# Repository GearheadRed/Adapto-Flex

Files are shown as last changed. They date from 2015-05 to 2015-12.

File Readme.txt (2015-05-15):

Behold The ADAPTO FLEX!! http://reprap.org/wiki/Adapto_Flex
	Originated from the Adapto https://github.com/rotorit/Adapto

The thought behind the Adapto Flex is to support a more flexible variety of tool heads(thus Adapto Flex).

Currently the paste extruder mount and support for Mutley's Flex3Drive system(http://mutley3d.com/Flex3Drive/) exist in working complete tool head options. In the pipeline for mountable tool heads will be a dual extruder configuration, single extruder configuration, pen holder, and cable driven dremel mount(more suggestions and contributions welcome).

There are design changes with the Adapto Flex, notably implementing the Vertical X Standard(http://reprap.org/wiki/Vertical_X_Axis_Standard) and moving the Z axis smooth rods to the sides of the Z frame instead of in front of the Z frame. This has allowed for shrinking the X ends making them stronger with less material use, and relocating the belt and drive motor position to run between the X smooth rods.

The X carriage is a flat plate style with four bolt holes. This allows for mounting a variety of tool heads increasing the printers versatility. It is suggested to use a SmoothieBoard with the printer and leveraging the ability to swap out config files quickly and easily per tool head setup instead of having to re-flash the controller firmware each time you swap tool heads.

This design still retains the ability to use either Alu extrusions (20x20mm), wood, alu, acryl plates or plates made out of any material(if it is stiff enough). Smooth rods can still be of any length, however the upper cross frame piece must be the same length as the front and rear lower frame pieces now(X axis). It is recommended to use 20x20mm aluminum T-slot extrusion for the frame and 10mm smooth rods.

Example STLs have been provided to view the parts on github. Most parts are based on RoTorITs design but either combined to reduce part count, save plastic, or make the design more versatile. A few parts are t00ties designs or t00ties code re-structured to handle the central config file better(these files retain t00ties copyright headings in them).

On the todo list is:
  -Endstop holders

ENJOY!

Making the STLs
---------------
Edit ./inc/configuration.scad to suit your needs. Check the resulting parts for sanity.

On linux make the stls by typing one of
make -k
make -k -j12

If openscad is in your path this should result in lots of new files in the "output" directory.
The _x# in the file names is the amount of a given part that needs to be printed.

Creative Commons - GNU GPL license

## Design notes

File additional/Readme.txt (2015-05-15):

Additional Component parts and templates.

Files - Description

bedBlockBasic_x4.scad	-	basic corner blocks to support heated pcb and glass
bedBlockRetainer_x2.scad-	corner blocks with retaining tabs to hold down heated pcb and glass
bedHoles.dxf		-	defines holes for the base bed plate
bedHoles.scad		-	defines holes for the base bed plate
cornerBrace_x8.scad	-	corner braces for aluminum extrusions(metal corner braces are suggested)
Extruder.scad		-	minimalistic direct drive extruder[STILL IN DEVELOPMENT DO NOT USE]
Flex3DriveFan.scad	-	fan mount for use with Flex3DriveMount
Flex3DriveMount.scad	-	mount design to hold Mutleys Flex3Drive system to the xCarriage
IndicatorMount.scad	-	mount for basic digital/dial indicator, clamps to x carriage rods
SyringeMount.scad	-	holds a syringe to the xCarriage
zEndstop.scad		-	quick and dirty z endstop bracket

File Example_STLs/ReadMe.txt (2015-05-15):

These STLs were generated via openSCAD with the below settings in the ./inc/configuration.scad file.

!!!This is not likely default configuration for most users due to the ACME rod specs for the z axis but applies to GearheadRed's printer configuration specifically.

//====================//
// Basic Config Items //
//====================//
smoothRod=10;			// diameter of smooth rods in mm
linearBearing=lm10uu;		// change this to the linear bearing you are using from the definitions section
zRod=ACME14;			// change this to the z threaded rod you are using from the definitions section
zRodnut=ACME14nut;		// change this to the z nut you are using from the definitions section
zRodnutThickness=ACME14nutThickness;	// change this to the z nut thickness you are using from the definitions section

//=======================//
// Advanced Config Items //
//=======================//
$fn=200;			// default resolution for parts, decrease if part compiling or stl/gcode is unmanageable
thickness=5;			// thickness of walls etc. in parts
smoothRodOffset=thickness*2+2+smoothRod/2;	// how far the centre of the z smooth rods are from the frame

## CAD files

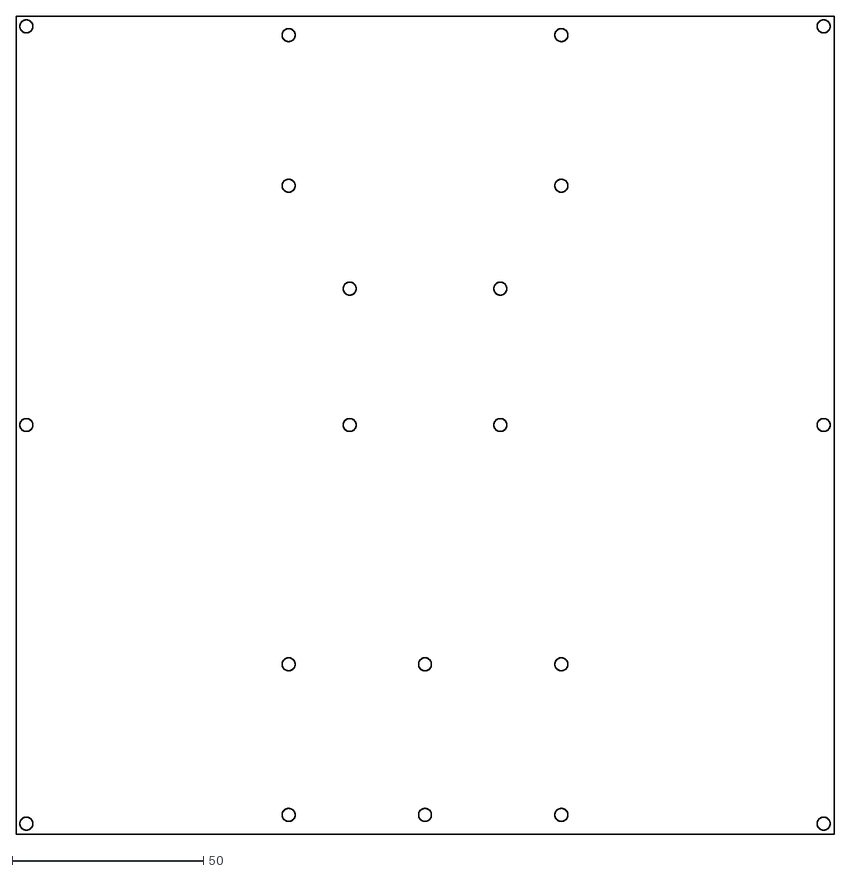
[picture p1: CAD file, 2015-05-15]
additional/bedHoles.dxf
214.0 x 214.0

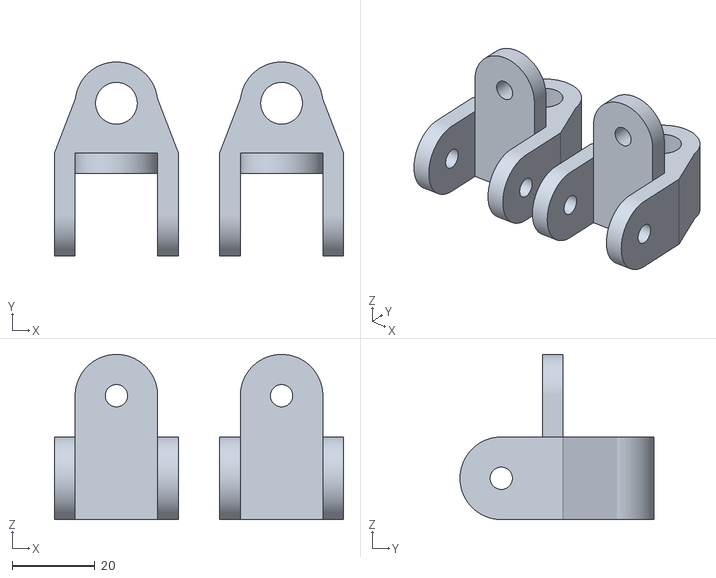
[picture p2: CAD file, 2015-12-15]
Example_STLs/zUpper_x1.stl
70.0 x 47.0 x 40.0

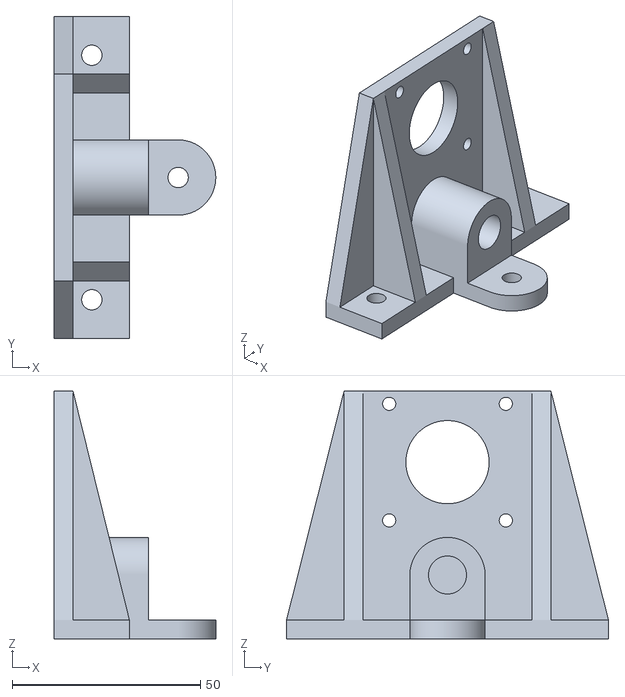
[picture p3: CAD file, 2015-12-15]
Example_STLs/zMotor_x2.stl
43.0 x 85.6 x 65.9

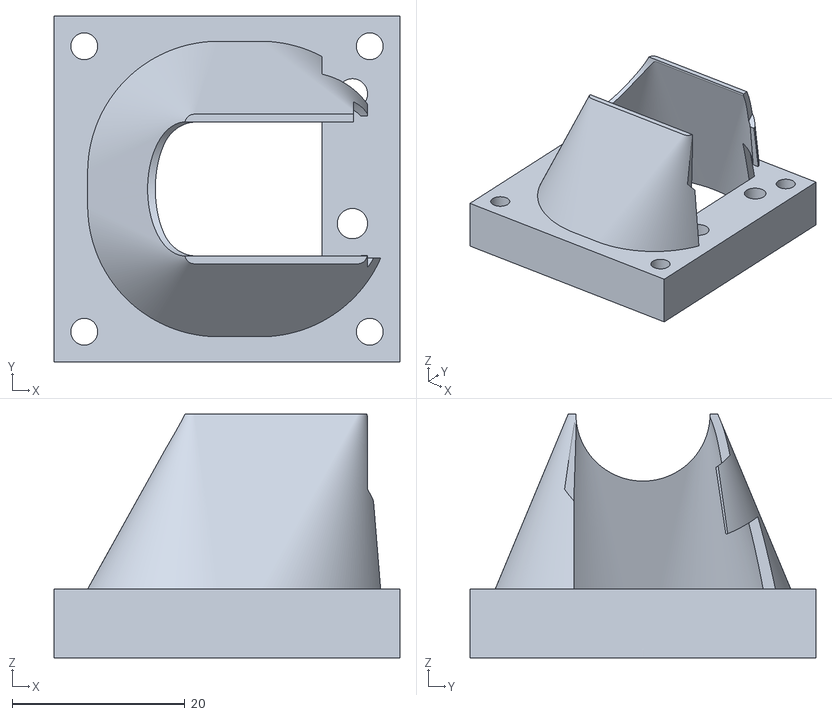
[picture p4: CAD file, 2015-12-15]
Example_STLs/Flex3DriveV2Fan.stl
40.0 x 40.0 x 28.2

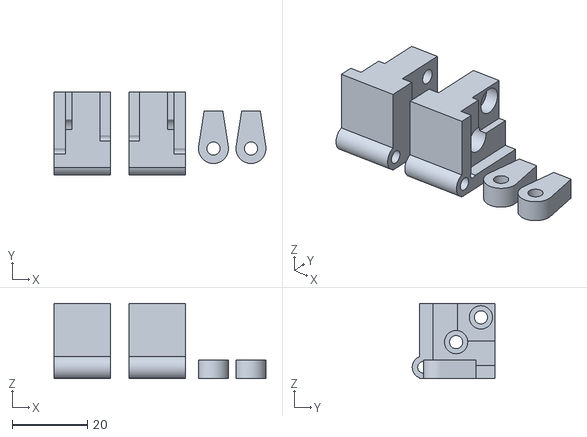
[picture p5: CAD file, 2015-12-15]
Example_STLs/bedBlockRetainer_custom.stl
56.5 x 22.0 x 20.0

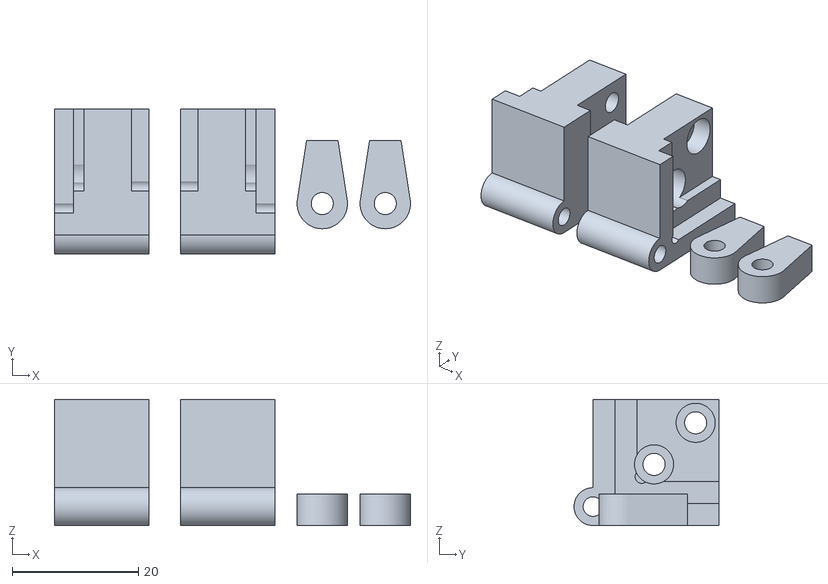
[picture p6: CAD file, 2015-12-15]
Example_STLs/bedBlockRetainer_x2.stl
56.5 x 23.0 x 20.0

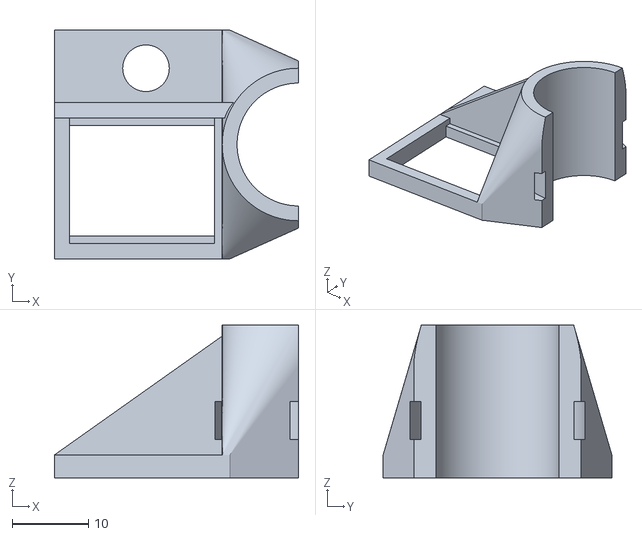
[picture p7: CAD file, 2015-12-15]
Example_STLs/hotendPower.stl
32.0 x 30.0 x 20.0

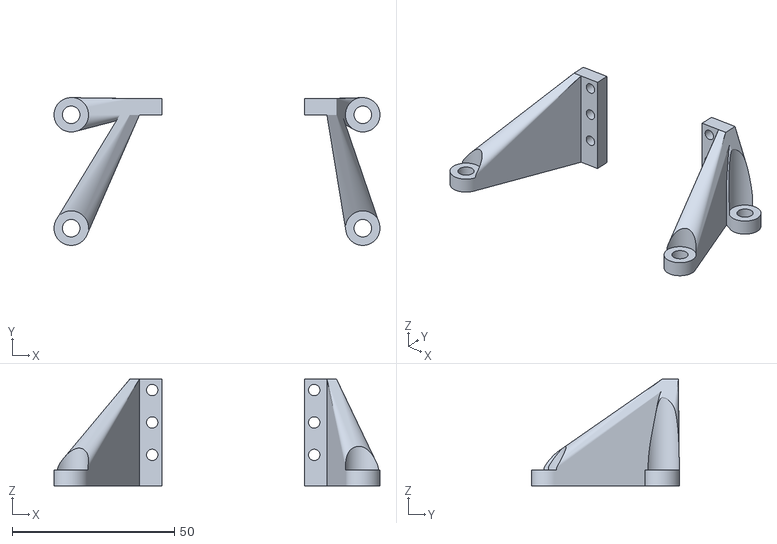
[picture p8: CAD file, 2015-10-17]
Example_STLs/Flex3DriveV2Mount.stl
100.6 x 45.6 x 33.0

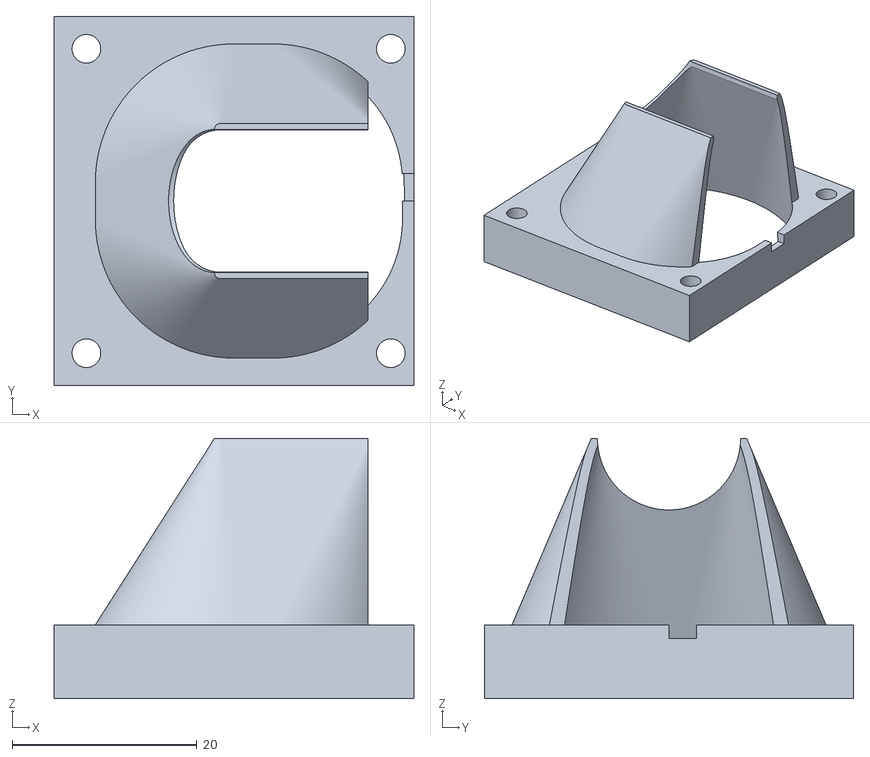
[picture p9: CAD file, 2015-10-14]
Example_STLs/Flex3DriveV1Fan.stl
39.0 x 40.0 x 28.2

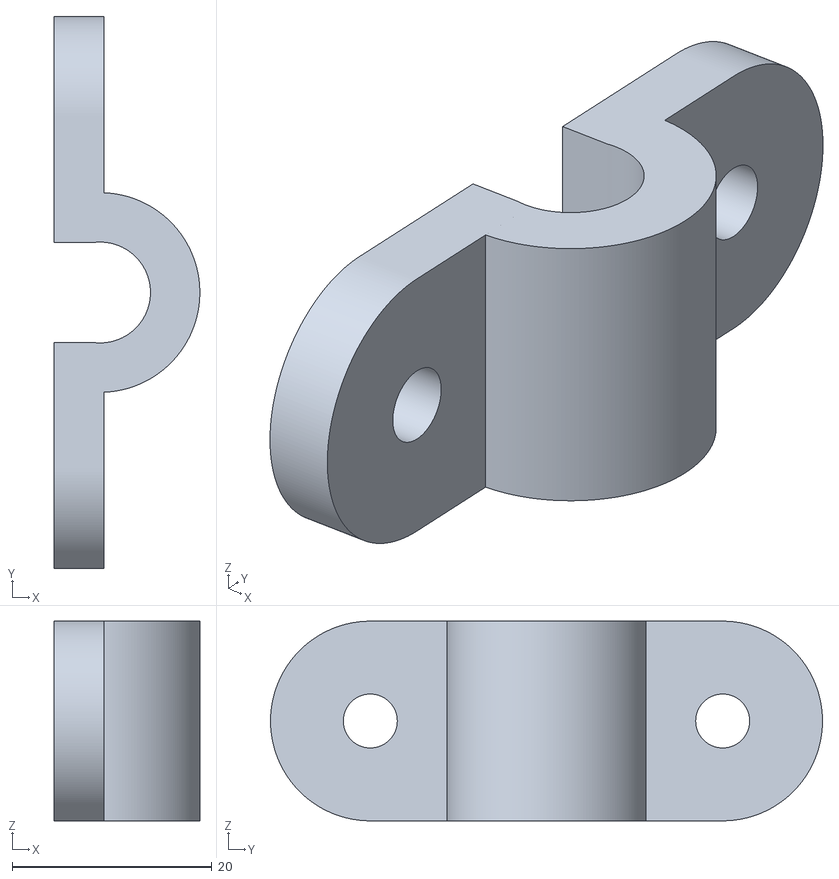
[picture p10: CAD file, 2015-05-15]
Example_STLs/yClamp_x4.stl
14.6 x 55.3 x 20.0

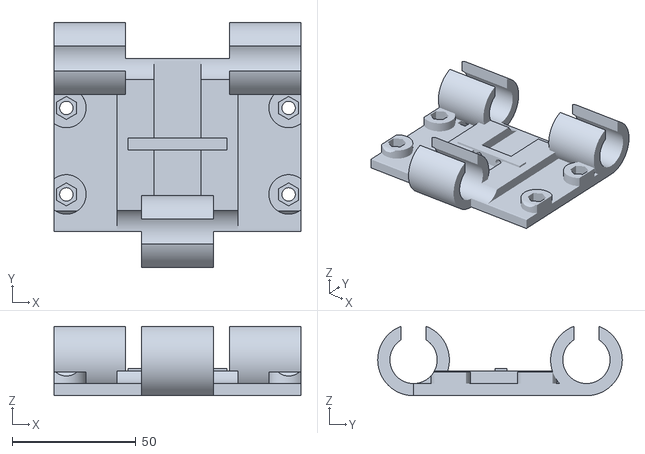
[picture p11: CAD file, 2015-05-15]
Example_STLs/xCarriage_x1.stl
100.0 x 99.0 x 28.1

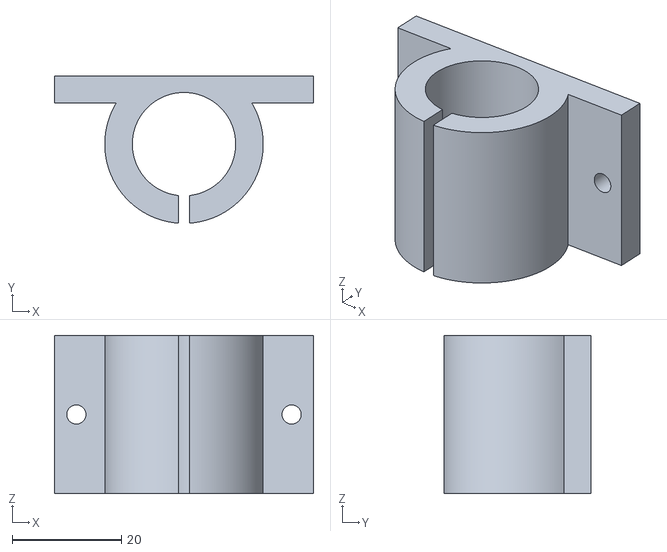
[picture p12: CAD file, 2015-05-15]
Example_STLs/yBearing_x4.stl
47.4 x 27.0 x 29.0

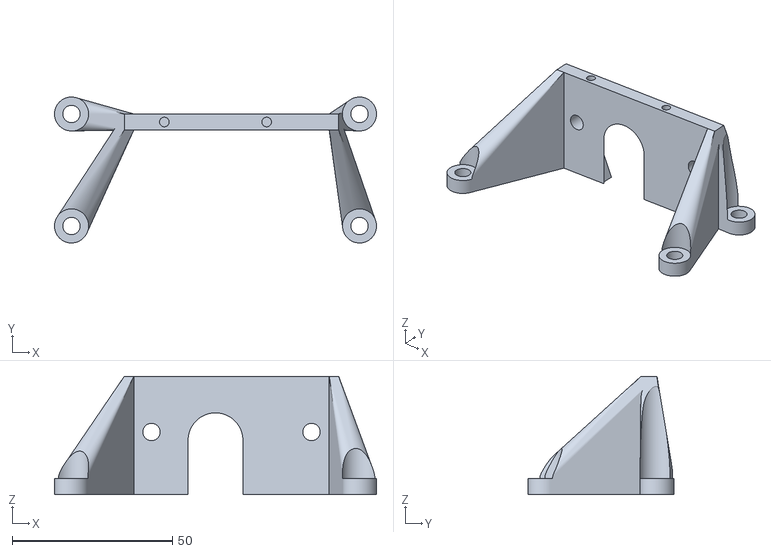
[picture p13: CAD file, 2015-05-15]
Example_STLs/Flex3DriveV1Mount.stl
100.6 x 45.6 x 37.0

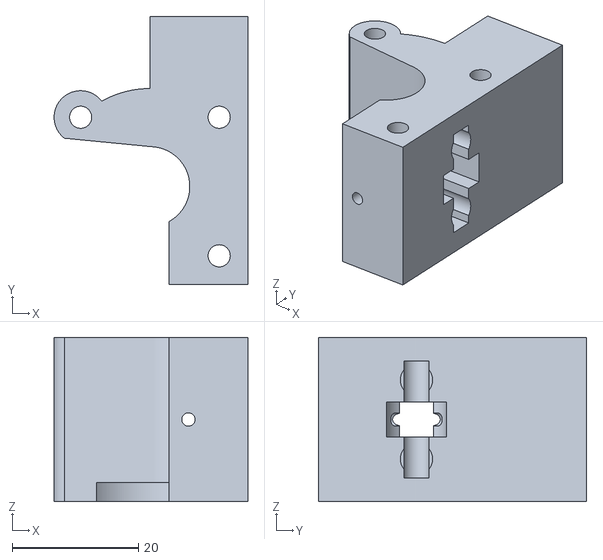
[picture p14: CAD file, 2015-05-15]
Example_STLs/Extruder_demo.stl
30.7 x 42.4 x 26.0

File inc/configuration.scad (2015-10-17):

// Adapto Flex is licensed under the Creative Commons - GNU GPL license.
// http://creativecommons.org/licenses/GPL/2.0/
// Originated from Adapto https://github.com/rotorit/Adapto

//==========================================================================//
// Configuration file for Adapto Flex OpenSCAD files                        //
// Scroll past the definition section to change basic and advanced settings //
//==========================================================================//

//====================//
// Definition Section //
//====================//
// Frame and Walls
// frameX and frameY are the dimensions of the frame material when viewed on end(the end of an extrusion looks roughly like an X)
// frameX is the width of the frame material
// frameY is the height of the frame material
//   x
//  [ ]y
// these are used to find offsets for screw placing so screws meet the (slot in the) middle of the frame
frameX=20;// width of the frame material(alu, wood etc.)
frameY=20;// height of the frame material

// Print the hole_calibration.scad object to dial in the next 6 settings
// Google found http://www.fairburyfastener.com/xdims_metric_nuts.htm
M8=8.4;// diameter of M8 threaded rod
M5=5.3;// diameter of M5 threaded rod
M3=3.4;// diameter of M3 threaded rod
M8nut=13;// diameter of M8 nut flat to flat
M5nut=8;// diameter of M5 nut flat to flat
M3nut=5.6;// diameter of M3 nut flat to flat

M8nutThickness=6.8;// thickness of a standard M8 nut(nylock is 8mm)
M5nutThickness=4.7;// thickness of a standard M5 nut(nylock is 5mm)
M3nutThickness=2.4;// thickness of a standard M3 nut

// Acme Linear Screw and Nut
ACME14=6.5;// diameter of 1/4 inch ACME threaded rod in mm
ACME14nut=12.8;// diameter of ACME 1/4 inch nut flat to flat in mm
ACME14nutThickness=6.5;// thickness of ACME 1/4 inch nut in mm

// Linear Bearings
// format is IDxODxL
lm8uu=[8, 15, 24];
lm10uu=[10, 19, 29];
lm10luu=[10, 19, 55];
lm12uu=[12, 21, 30];

//rotary bearings
// format is IDxODxL
FL623=[3, 10, 4];
MF204=[4, 10, 4];
MF126=[6, 12, 4];
rotaryBearing=MF126;// for readability(can be changed if other bearings are used

//====================//
// Basic Config Items //
//====================//
smoothRod=10;				// diameter of smooth rods in mm
linearBearing=lm10uu;	// change this to the linear bearing you are using from the definitions section
zRod=ACME14;				// change this to the z threaded rod you are using from the definitions section
zRodnut=ACME14nut;		// change this to the z nut you are using from the definitions section
zRodnutThickness=ACME14nutThickness;	// change this to the z nut thickness you are using from the definitions section

//=======================//
// Advanced Config Items //
//=======================//
$fn=250;		// default resolution for parts, decrease if part compiling or stl/gcode is unmanageable
thickness=5;		// thickness of walls etc. in parts
pullyDiameter=12.2;	// GT2-20 toothed section diameter
smoothRodOffset=thickness*2+2+smoothRod/2;	// how far the centre of the z smooth rods are from the frame
Flex3Drive=true;	// If the Flex3Drive is used
carriageDrop=15;	// From center of carriage to top mounting surface on extruder mounts

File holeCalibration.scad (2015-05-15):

// Adapto Flex is licensed under the Creative Commons - GNU GPL license.
// http://creativecommons.org/licenses/GPL/2.0/
// Originated from Adapto https://github.com/rotorit/Adapto
include <./inc/configuration.scad>
use <./inc/polyarc.scad>

// hole size calibration object
// M8 has a block on top of the arch
// Order goes from block on top of M8, M5, M3, zRod
echo("M3=", M3);
echo("M5=", M5);
echo("M8=", M8);
echo("zRod=", zRod);
echo("M3nut=", M3nut);
echo("M5nut=", M5nut);
echo("M8nut=", M8nut);
echo("zRodnut=", zRodnut);

holes();
translate([0, 2*thickness+M8, thickness+M8/2]) rotate([-90, 0, 0]) holes();

module holes(){

	difference(){

		union(){
			// the arches
			// M8+block
			translate([0, 0, 0])
				polycyl(d=M8+thickness*2, h=thickness);
			translate([-thickness/2, -thickness/2-M8, 0])
				cube([thickness, thickness, thickness]);

			// M5
			translate([M8/2+1.5*thickness+M5/2, M5/2, 0])
				polycyl(d=M5+thickness*2, h=thickness);

			// M3
			translate([M8/2+1.5*thickness+M5/2+2*thickness+M3/2, M3, 0])
				polycyl(d=M3+thickness*2, h=thickness);

			// zRod
			translate([M8/2+1.5*thickness+M5/2+2*thickness+M3/2+2*thickness+(zRod+2)/2, 0,0])
				polycyl(d=zRod+2+thickness*2, h=thickness);

			// flat base
			hull(){
				translate([-thickness-M8/2, 0, 0])
					cube([thickness, thickness+M8/2, thickness]);
				translate([M8/2+1.5*thickness+M5/2+2*thickness+M3/2+2*thickness+zRod+2, 0, 0])
					cube([thickness, thickness+M8/2, thickness]);
			}

		}// end union

		// the holes and nut traps
		// M8
		translate([0, 0, -1])
			polyhole(d=M8, h=thickness/2+2);
		translate([0, 0, thickness/2])
			polynut(d=M8nut, h=thickness/2+2);

		// M5
		translate([M8/2+1.5*thickness+M5/2, M5/2, -1])
			polyhole(d=M5, h=thickness/2+2);
		translate([M8/2+1.5*thickness+M5/2, M5/2, thickness/2])
			polynut(d=M5nut, h=thickness/2+2);

		// M3
		translate([M8/2+1.5*thickness+M5/2+2*thickness+M3/2, M3, -1])
			polyhole(d=M3, h=thickness/2+2);
		translate([M8/2+1.5*thickness+M5/2+2*thickness+M3/2, M3, thickness/2])
			polynut(d=M3nut, h=thickness/2+2);

		// zRod
		translate([M8/2+1.5*thickness+M5/2+2*thickness+M3/2+2*thickness+(zRod+2)/2, 0, -1])
			polyhole(d=zRod, h=thickness/2+2);
		translate([M8/2+1.5*thickness+M5/2+2*thickness+M3/2+2*thickness+(zRod+2)/2, 0, thickness/2])
			polynut(d=zRodnut, h=thickness/2+2);

		// the flat base
		hull(){
			translate([-thickness-M8/2, thickness+M8/2, -1])
				cube([thickness, thickness, thickness+2]);
			translate([M8/2+1.5*thickness+M5/2+2*thickness+M3/2+2*thickness+zRod+2, thickness+M8/2, -1])
				cube([thickness, thickness, thickness+2]);
		}

	}// end difference

}

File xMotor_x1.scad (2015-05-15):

// Adapto Flex is licensed under the Creative Commons - GNU GPL license.
// http://creativecommons.org/licenses/GPL/2.0/
// Originated from Adapto https://github.com/rotorit/Adapto
include <./inc/configuration.scad>
use <./inc/polyarc.scad>
use <./inc/xBacker.scad>

rotate([0, -90, 180])
    xMotor();

module xMotor(){

    difference(){

        union(){

            xBacker();// import the base x backing model

            // nema mounting
            hull(){
                translate([-88/2, 30-18/2-6,  thickness*2+linearBearing[1]])
                    cube([88, 1, thickness-1]);
                translate([-88/2, 30+18/2,  thickness*2+linearBearing[1]])
                    cube([88, 1, thickness+1]);

                translate([0, 30+zRodnut/2+thickness+M3, thickness*2+linearBearing[1]])
                    polycyl(d=M3+thickness*2, h=thickness+1);

                translate([1.41*31/2, 30+zRodnut/2+thickness+M3+1.41*31/2, thickness*2+linearBearing[1]])
                    polycyl(d=M3+thickness*2, h=thickness+1);
                translate([-1.41*31/2, 30+zRodnut/2+thickness+M3+1.41*31/2, thickness*2+linearBearing[1]])
                    polycyl(d=M3+thickness*2, h=thickness+1);
            }
    
            // endstop adjust screw
            hull(){
                translate([-88/2, linearBearing[1]/2, -thickness])
                    cube([thickness, thickness, thickness]);
                translate([-88/2, linearBearing[1]/2-thickness, 0])
                    cube([thickness, thickness*3, 1]);
            }

        }// end union

        // nema bolt holes
        translate([0, 30+zRodnut/2+thickness+M3, thickness*2+linearBearing[1]-1])
            polyhole(d=M3, h=thickness+3);
        translate([1.41*31/2, 30+zRodnut/2+thickness+M3+1.41*31/2, thickness*2+linearBearing[1]-1])
            polyhole(d=M3, h=thickness+3);
        translate([-1.41*31/2, 30+zRodnut/2+thickness+M3+1.41*31/2, thickness*2+linearBearing[1]-1])
            polyhole(d=M3, h=thickness+3);

        // nema center axle cutout
        hull(){
            translate([0, 30+zRodnut/2+thickness+M3+1.41*31/2, thickness*2+linearBearing[1]-1])
                polyhole(d=22, h=thickness+3);
            translate([0, 30+zRodnut/2+thickness+M3+1.41*31/2, thickness*2+linearBearing[1]-1])
                rotate([0, 0, 45])
                cube([31*2, 31*2, thickness+3]);
        }

        // nema motor shaft and pulley
        %translate([0, 30+zRodnut/2+thickness+M3+1.41*31/2, thickness*2+linearBearing[1]])
            polyhole(d=5, h=thickness+18);
        %translate([0, 30+zRodnut/2+thickness+M3+1.41*31/2, thickness*2+linearBearing[1]+thickness*2+7])
            polyhole(d=15, h=1);
        %translate([0, 30+zRodnut/2+thickness+M3+1.41*31/2, thickness*2+linearBearing[1]+thickness*2])
            polyhole(d=pullyDiameter, h=7);
        %translate([0, 30+zRodnut/2+thickness+M3+1.41*31/2, thickness*2+linearBearing[1]+thickness*2-5])
            polyhole(d=15, h=5);
        %translate([0, 30+zRodnut/2, -45+thickness*2+linearBearing[1]])
            rotate([0, 0, 45])
            cube([45, 45, 45]);

        // make sure the holes for the screws to hold the x smooth rods in place remain clear
        translate([70/2, 30-18/2, -1])
            polyhole(d=M3nut, h=thickness*2+linearBearing[1]+thickness+1);
        mirror([1,0,0])
            translate([70/2, 30-18/2, -1])
                polyhole(d=M3nut, h=thickness*2+linearBearing[1]+thickness+1);//
        translate([70/2, 30-18/2, thickness*2+linearBearing[1]+thickness-1])
            polyhole(d=M3, h=thickness+2+smoothRod/2);
        mirror([1,0,0])
            translate([70/2, 30-18/2, thickness*2+linearBearing[1]+thickness-1])
                polyhole(d=M3, h=thickness+2+smoothRod/2);

        // endstop adjust screw
        translate([-88/2+1.3, linearBearing[1]/2+thickness/2, -thickness/2])
            rotate([0, 90, 0])
            polyhole(d=M3, h=thickness+2);
        translate([-88/2+thickness-1, linearBearing[1]/2+thickness/2, -thickness/2])
            rotate([0, 90, 0])
            polynut(d=M3nut, h=M3nutThickness);
        translate([-88/2-M3nutThickness+1, linearBearing[1]/2+thickness/2, -thickness/2])
            rotate([0, 90, 0])
            polynut(d=M3nut, h=M3nutThickness);

    }// end difference

}

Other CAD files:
Example_STLs/cornerBrace_x8.stl
Example_STLs/SyringeMount.stl
Example_STLs/zEndstop.stl
Example_STLs/holeCalibration.stl
yMotor_x1.scad
Example_STLs/baseFoot_x4.stl
Example_STLs/bedBlockBasic_x4.stl
Example_STLs/xBeltTensioner_x1.stl
Example_STLs/xMotor_x1.stl
Example_STLs/yBlock_x1.stl
Example_STLs/yIdler_x1.stl
Example_STLs/yMotor_x1.stl
additional/Extruder.scad
additional/Flex3DriveV1Fan.scad
additional/Flex3DriveV1Mount.scad
additional/Flex3DriveV2Fan.scad
additional/Flex3DriveV2Mount.scad
additional/IndicatorMount.scad
additional/SyringeMount.scad
additional/bedBlockBasic_x4.scad
additional/bedBlockRetainer_custom.scad
additional/bedBlockRetainer_x2.scad
additional/bedHoles.scad
additional/cornerBrace_x8.scad
additional/hotendPower.scad
additional/zEndstop.scad
baseFoot_x4.scad
inc/polyarc.scad
inc/xBacker.scad
xBeltTensioner_x1.scad
xCarriage_x1.scad
xIdler_x1.scad
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

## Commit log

2015-05-15 Populating Repo
    Populating repo with files.
    [Extruder.scad, Extruder_demo.stl, Flex3DriveFan.scad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]
2015-10-08 Adding data for new Flex3Drive
    V2 of Flex3Drive includes its own fan mount and has more mounting holes.
    Adjusted the bracket for this and renamed the fan shroud to indicate
    that it is for V1 Flex3Drive mount.
    [Flex3DriveV1Fan.scad, Flex3DriveV1Fan.stl, Flex3DriveV1Mount.scad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]
2015-10-14 Adding fan shroud for Flex3Drive v2
    fan shroud for flex 3 drive v2 when used with a pico hotend
    [Flex3DriveV2Fan.scad]
2015-10-14 Finished up Flex3Drive fan mount for Pico
    [Flex3DriveV2Fan.scad, Flex3DriveV2Fan.stl]
2015-10-14 rotated Flex3Drive v1 fan shroud for better printing orientation
    [Flex3DriveV1Fan.scad, Flex3DriveV1Fan.stl]
2015-10-14 Adjusted for slot mount plate
    fan shroud was interfering with slot mount. fixed.
    [Flex3DriveV2Fan.scad, Flex3DriveV2Fan.stl]
2015-10-17 Made mount height for extruder variable.
    Needed to make the mount point for extruder variable to handle whatever
    height nozzle life may throw at it.
    [Flex3DriveV1Mount.scad, Flex3DriveV2Mount.scad, Flex3DriveV2Mount.stl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]
2015-10-17 Printability
    Fixed some clearance issues and eliminated some un-necessary finer
    edges.
    [Flex3DriveV2Fan.scad, Flex3DriveV2Fan.stl]
2015-12-15 Added and updated
    added an additional part and updated a few others
    [Flex3DriveV2Fan.scad, Flex3DriveV2Fan.stl, bedBlockRetainer_custom.scad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]
2015-12-15 Adjustments
    Adjusted the z motor mount for more rod clearance and made the z uppers
    more robust. Eliminated the alternate z upper code.
    [zMotor_x2.scad, zMotor_x2.stl, zUpper_x1.scad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]
